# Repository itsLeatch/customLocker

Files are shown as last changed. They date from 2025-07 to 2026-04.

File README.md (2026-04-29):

# customLocker
This project is an electrically locked box. You can safely store things that you are addicted to inside it and unlock it by reaching a particular goal. I'm going to put sweets in it and unlock the box once I've reached my daily calorie target on my smartwatch. Inside the box is a load cell that can roughly detect the amount of sweets taken out. In addition to that, there is a wireless charger, that will charge e.g. your phone while beeing busy. 
## Why I made this project
I often find myself looking at my phone a lot when I'm busy, which slows me down. Furthermore, I also want to do more sport. With the box, I can combine these things and create my first PCB, build a large 3D model, and learn many other skills.
## Showcase
https://github.com/user-attachments/assets/28022000-88c3-4b23-8f9c-2944c17416d4

## Pictures
### 3D-Model


### PCB-Front


### PCB-Back


## Wiring
servo motor: connect the red cable to +5v
hall effect sensor: when facing the smaller side the left once is +5v, the middle one GND and the right one signal
HX711: this board is solderd directly on the PCB in the only possible direction
power: connect the 5V of the USB-C connector with the +5V on the board and the +5V on the wireless charger, same for GND
## BOM
### Aliexpress
| Description | Link | price in USD |
|---|---|---|
| ESP32-32D to control everything | https://de.aliexpress.com/item/4000093185394.html?spm=a2g0o.cart.0.0.b1964ae4QiPiLO&mp=1&gatewayAdapt=glo2deu | 3,56 |
| load cell (5KG AND HX711) to detect the amount of removed items | https://de.aliexpress.com/item/4001274733879.html?spm=a2g0o.cart.0.0.b1964ae4QiPiLO&mp=1&gatewayAdapt=glo2deu | 1,9 |
| 0.96 inch display (white) to display information such as left time, calorien... | https://de.aliexpress.com/item/1005006141235306.html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 | 1,97 |
| servo motor (360°) to lock/open the box | https://de.aliexpress.com/item/1005007173214082.html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 | 1,8 |
| passive buzzer to notify the user | https://de.aliexpress.com/item/1005008825917787.html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 | 1,86 |
| keys (blue) for user inputs | https://de.aliexpress.com/item/1005004341695529.html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 | 1,62 |
| key caps (red) for the keys | https://de.aliexpress.com/item/1005007209930123.html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 | 7,26 |
| wireless charger (b) if the smartphone or simular is in the box | https://de.aliexpress.com/item/1005006386722006.html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 | 5,76 |
| hall effect sensor (47E) to check if the box is open or closed | https://de.aliexpress.com/item/1005008647103022.html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 | 1,8 |
| magnetic tape (10mmx1mm, 1 Meter) for the hall effect sensor | https://de.aliexpress.com/item/1005006757451588.html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 | 2,39 |
| USB-C PCB for power | https://de.aliexpress.com/item/1005009193894473.html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 | 1,15 |
| connector pins (each color) to connect the components to the PCB | https://de.aliexpress.com/item/1005007324368709.html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 | 1,36 |
| some cables (M-F-20pin) to connect the components as well | https://de.aliexpress.com/item/1005007805542492.html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 | 1,24 |
| M4x16mm screws to mount most of the components | https://de.aliexpress.com/item/1005006674812661.html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 | 1,77 |
| m4 threaded inserts (OD 6mm, lenght 6mm) for the screws | https://de.aliexpress.com/item/1005003582355741.html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 | 2,59 |
| M5x30 screws to mount the load cell and the opening mechanism of the box | https://de.aliexpress.com/item/1005006051322108.html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 | 3,26 |
| shipping cost to Germany | | 6,27 |
| total price for ALIEXPRESS | | 47,56 |
### local building center
| Description | price in €  |
|---|---|
| 2 pices M4 DIN9021 to spread the pressure over the box | 2X0,24=0,48 |
| 2 pices M5 DIN9021 to spread the pressure over the box | 2x0,29=0,58 |
| 2 pieces M5 domed cap nut | 2x0,49=0,98 |
| total price in € | 2,04€ |
| total price in $ (7/17/2025 at 4:44pm under: https://www.visa.de/support/verbraucher/visa-reiseservices/exchange-rate-calculator.html)  | 2,39$ |

### PCB from jlcpcp
| Description | price in $ |
|---|---|
| 2 pices M4 DIN9021 to spread the pressure over the box | 4 |
| shipping cost | 3,3 |
| total | 7,3 |

### total cost
| Description | price in $ |
|---|---|
| aliexpress | 47,56 |
| local building center | 2,39 |
| PCB | 7,3 |
| 3D-Filament | nothing - I have to use Printing Legion because I have no 3D-Printer yet 😥 |
| total | **57,25** |

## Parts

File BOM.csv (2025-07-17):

Description | Link | price in USD | Description | price in € | Description | price in $ | Description | price in $
ESP32-32D to control everything | https://de.aliexpress.com/item/4000093185394.html?mp=1 | 3,56 | 2 pices M4 DIN9021 to spread the pressure over the box | 2X0,24=0,48 | 2 pices M4 DIN9021 to spread the pressure over the box | 4 | aliexpress | 47,56
load cell (5KG AND HX711) to detect the amount of removed items | https://de.aliexpress.com/item/4001274733879.html?mp=1 | 1,9 | 2 pices M5 DIN9021 to spread the pressure over the box | 2x0,29=0,58 | shipping cost | 3,3 | local building center | 2,39
0.96 inch display (white) to display information such as left time, calorien... | https://de.aliexpress.com/item/1005006141235306.html?mp=1 | 1,97 | 2 pieces M5 domed cap nut | 2x0,49=0,98 | total | 7,3 | PCB | 7,3
servo motor (360°) to lock/open the box | https://de.aliexpress.com/item/1005007173214082.html?mp=1 | 1,8 | total price in € | 2,04€ |  |  | 3D-Filament | nothing - I have to use Printing Legion because I have no 3D-Printer yet 😥
passive buzzer to notify the user | https://de.aliexpress.com/item/1005008825917787.html?mp=1 | 1,86 | total price in $ (7/17/2025 at 4:44pm under: https://www.visa.de/support/verbraucher/visa-reiseservices/exchange-rate-calculator.html) | 2,39 |  |  | total | 57,25
keys (blue) for user inputs | https://de.aliexpress.com/item/1005004341695529.html?mp=1 | 1,62
key caps (red) for the keys | https://de.aliexpress.com/item/1005007209930123.html?mp=1 | 7,26
wireless charger (b) if the smartphone or simular is in the box | https://de.aliexpress.com/item/1005006386722006.html?mp=1 | 5,76
hall effect sensor (47E) to check if the box is open or closed | https://de.aliexpress.com/item/1005008647103022.html?mp=1 | 1,8
magnetic tape (10mmx1mm, 1 Meter) for the hall effect sensor | https://de.aliexpress.com/item/1005006757451588.html?mp=1 | 2,39
USB-C PCB for power | https://de.aliexpress.com/item/1005009193894473.html?mp=1 | 1,15
connector pins (each color) to connect the components to the PCB | https://de.aliexpress.com/item/1005007324368709.html?mp=1 | 1,36
some cables (M-F-20pin) to connect the components as well | https://de.aliexpress.com/item/1005007805542492.html?mp=1 | 1,24
M4x16mm screws to mount most of the components | https://de.aliexpress.com/item/1005006674812661.html?mp=1 | 1,77
m4 threaded inserts (OD 6mm, lenght 6mm) for the screws | https://de.aliexpress.com/item/1005003582355741.html?mp=1 | 2,59
M5x30 screws to mount the load cell and the opening mechanism of the box | https://de.aliexpress.com/item/1005006051322108.html?utparam-url=scene%3Asearch%7Cquery_from%3A | 3,26
shipping cost to Germany |  | 6,27
total price for ALIEXPRESS |  | 47,56

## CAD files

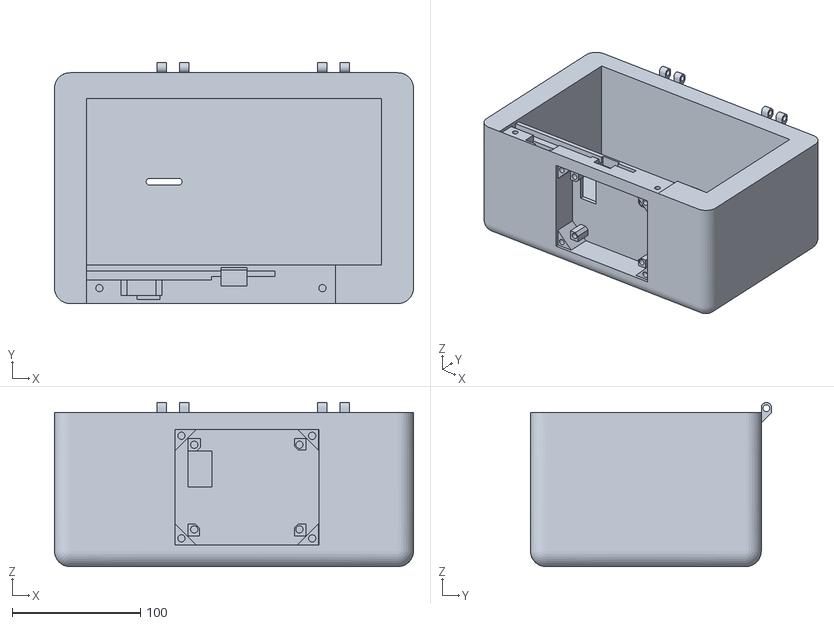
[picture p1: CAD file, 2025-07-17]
models/Box.stl
280.0 x 188.0 x 128.0

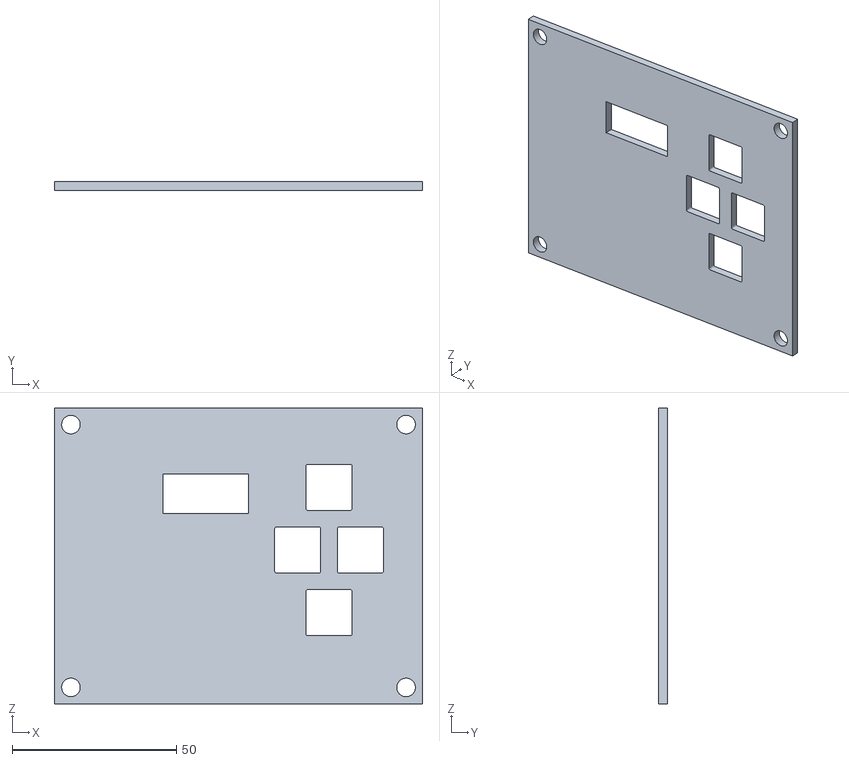
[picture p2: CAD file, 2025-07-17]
models/Front Cover.stl
112.0 x 2.80 x 90.0

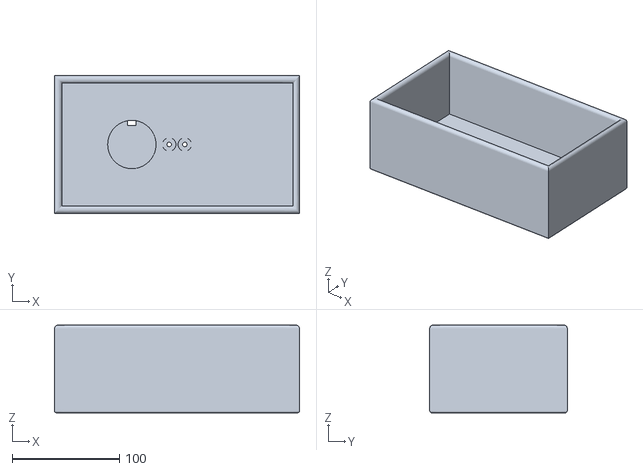
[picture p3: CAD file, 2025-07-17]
models/inner box.stl
228.0 x 128.0 x 81.8

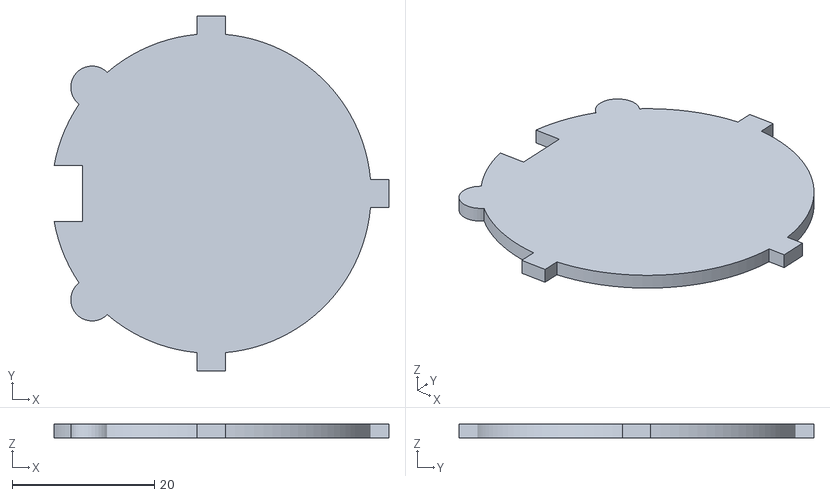
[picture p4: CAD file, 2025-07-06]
models/wireless charger cover.stl
47.2 x 50.0 x 2.00

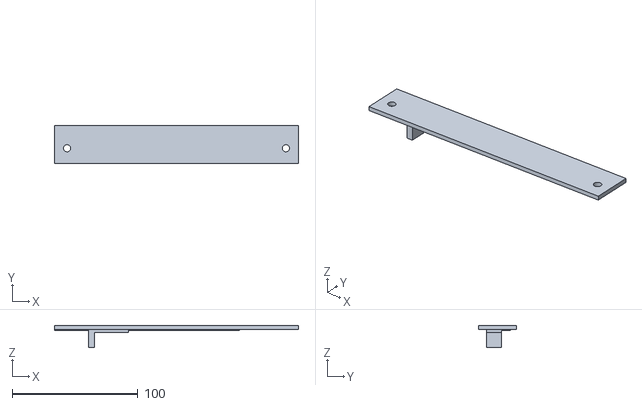
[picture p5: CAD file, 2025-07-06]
models/Gear Cover.stl
194.0 x 30.0 x 17.5

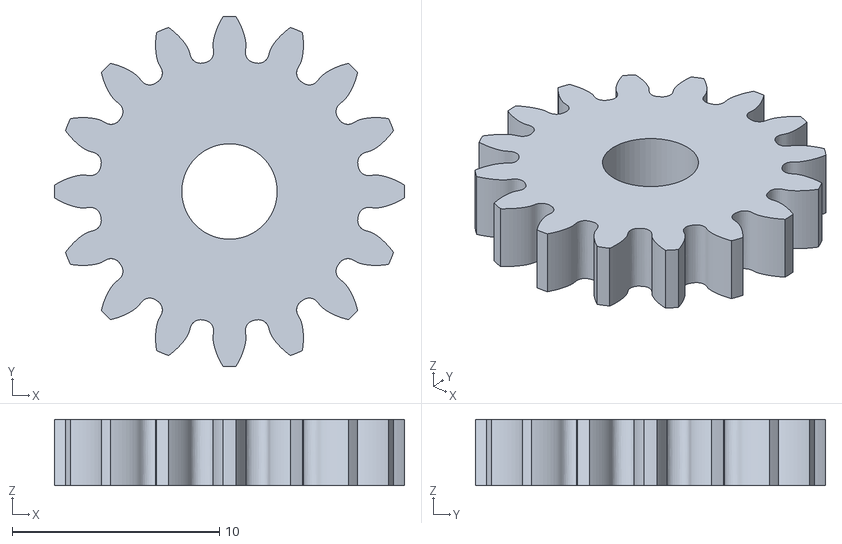
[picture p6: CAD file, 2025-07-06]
models/cog.stl
16.9 x 16.9 x 3.20

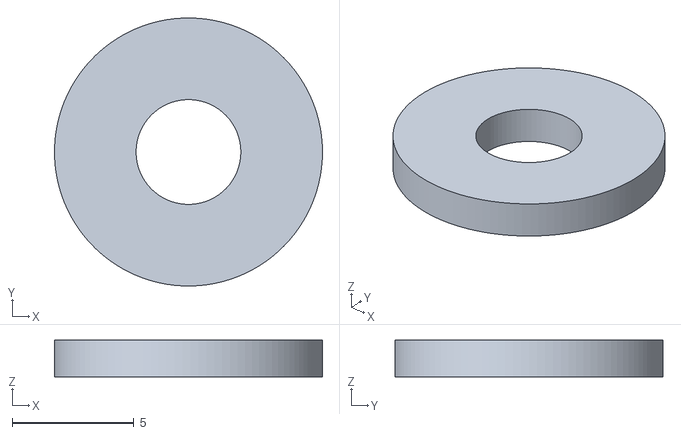
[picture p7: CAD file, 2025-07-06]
models/M4 connector 1.stl
11.0 x 11.0 x 1.50

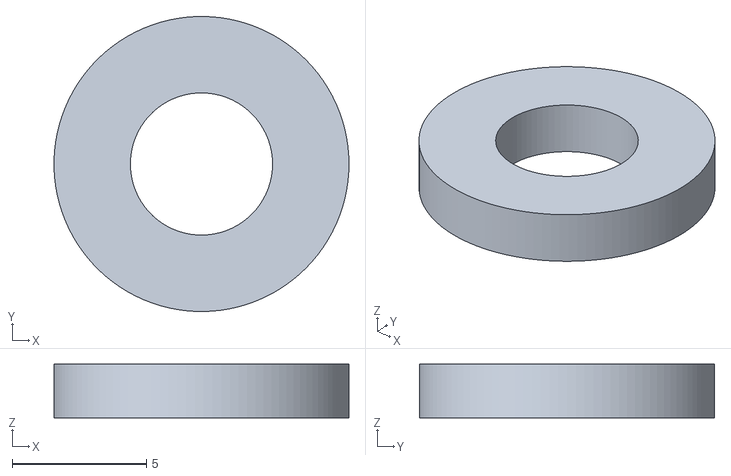
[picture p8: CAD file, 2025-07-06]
models/M5 connector 1.stl
11.0 x 11.0 x 2.00

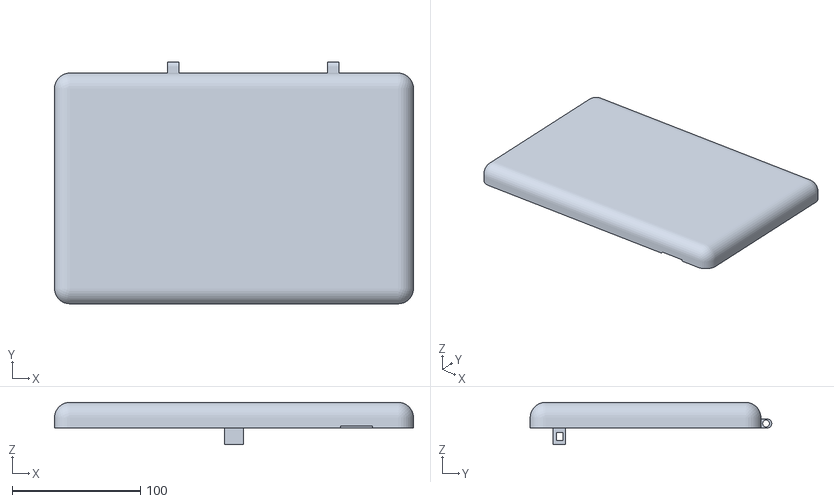
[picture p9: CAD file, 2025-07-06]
models/Box Cover.stl
280.0 x 188.5 x 33.0

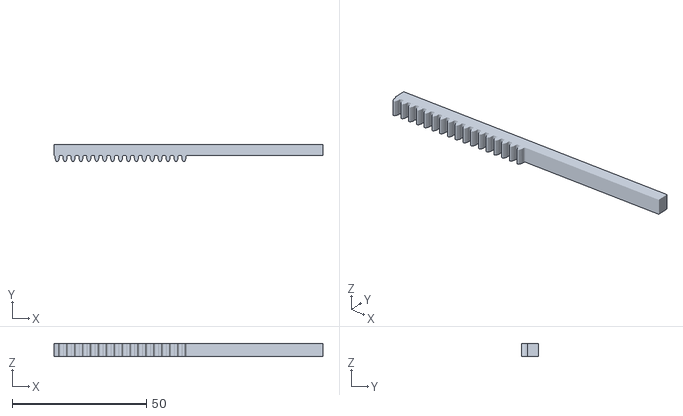
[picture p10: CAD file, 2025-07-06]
models/rack gear.stl
100.0 x 6.24 x 5.00

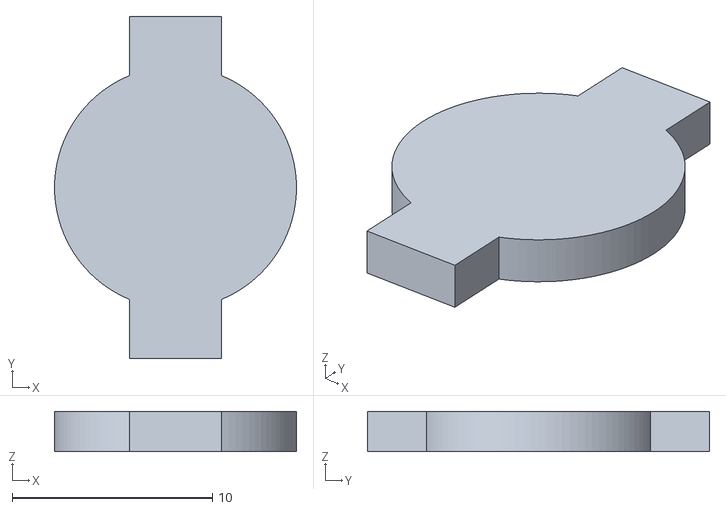
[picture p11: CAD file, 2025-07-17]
models/screw cover 1.stl
12.1 x 17.1 x 2.00

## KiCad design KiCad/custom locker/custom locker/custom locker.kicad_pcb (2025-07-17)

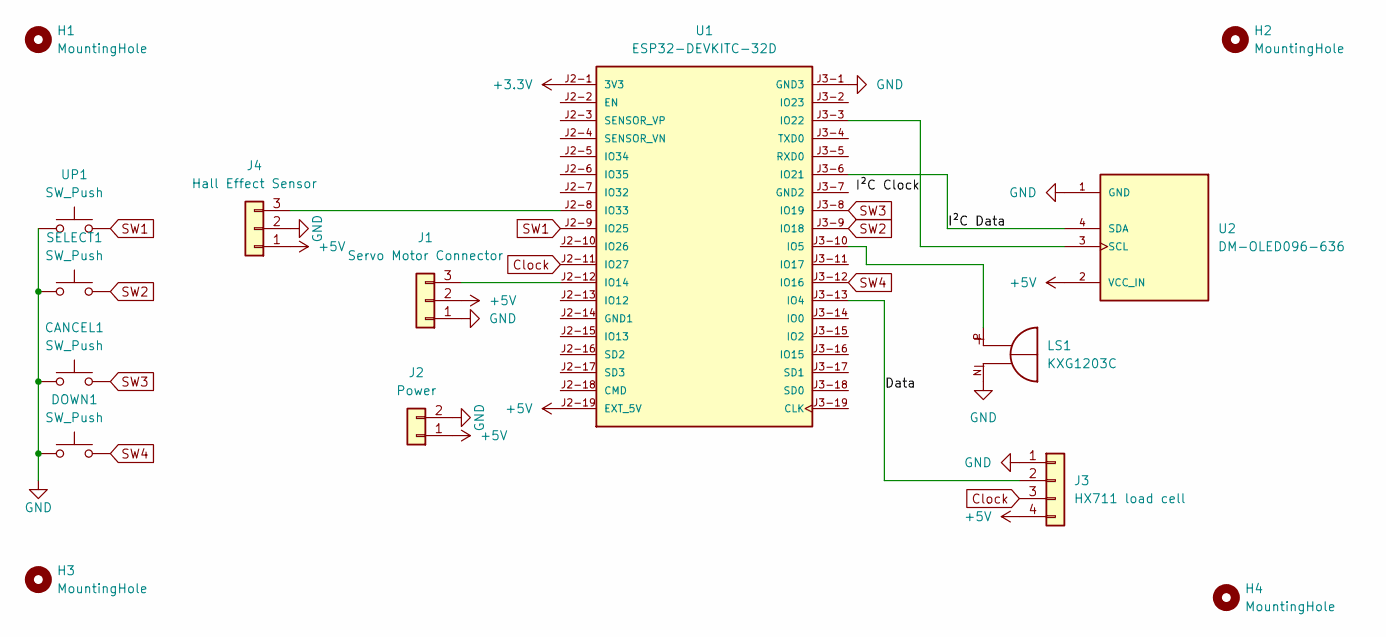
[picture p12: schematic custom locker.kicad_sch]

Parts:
CANCEL1: SW_Push; SW_Cherry_MX_1.00u_PCB
DOWN1: SW_Push; SW_Cherry_MX_1.00u_PCB
H1, H2, H3, H4: MountingHole; MountingHole_4.3mm_M4
J1: Servo Motor Connector; PinHeader_1x03_P2.54mm_Vertical
J2: Power; PinHeader_1x02_P2.54mm_Vertical
J3: HX711 load cell; PinHeader_1x04_P2.54mm_Vertical
J4: Hall Effect Sensor; PinHeader_1x03_P2.54mm_Vertical
LS1: KXG1203C; XDCR_KXG1203C; PARTREV 1.3
SELECT1: SW_Push; SW_Cherry_MX_1.00u_PCB
U1: ESP32-DEVKITC-32D; MODULE_ESP32-DEVKITC-32D; PARTREV V4
U2: DM-OLED096-636; MODULE_DM-OLED096-636; PARTREV 2018-09-10
UP1: SW_Push; SW_Cherry_MX_1.00u_PCB

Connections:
+3.3V: U1.J2-1 (3V3)
+5V: J1.2, J2.1, J3.4, J4.1, U1.J2-19 (EXT_5V), U2.2 (VCC_IN)
/Data: J3.2, U1.J3-13 (IO4)
/I²C Clock: U1.J3-3 (IO22), U2.3 (SCL)
/I²C Data: U1.J3-6 (IO21), U2.4 (SDA)
Clock: J3.3, U1.J2-11 (IO27)
GND: CANCEL1.1, DOWN1.1, J1.1, J2.2, J3.1, J4.2, LS1.N, SELECT1.1, U1.J3-1 (GND3), U2.1 (GND), UP1.1
unnamed: J1.3, U1.J2-12 (IO14)
unnamed: J4.3, U1.J2-8 (IO33)
unnamed: LS1.P, U1.J3-10 (IO5)
SW1: U1.J2-9 (IO25), UP1.2
SW2: SELECT1.2, U1.J3-9 (IO18)
SW3: CANCEL1.2, U1.J3-8 (IO19)
SW4: DOWN1.2, U1.J3-12 (IO16)

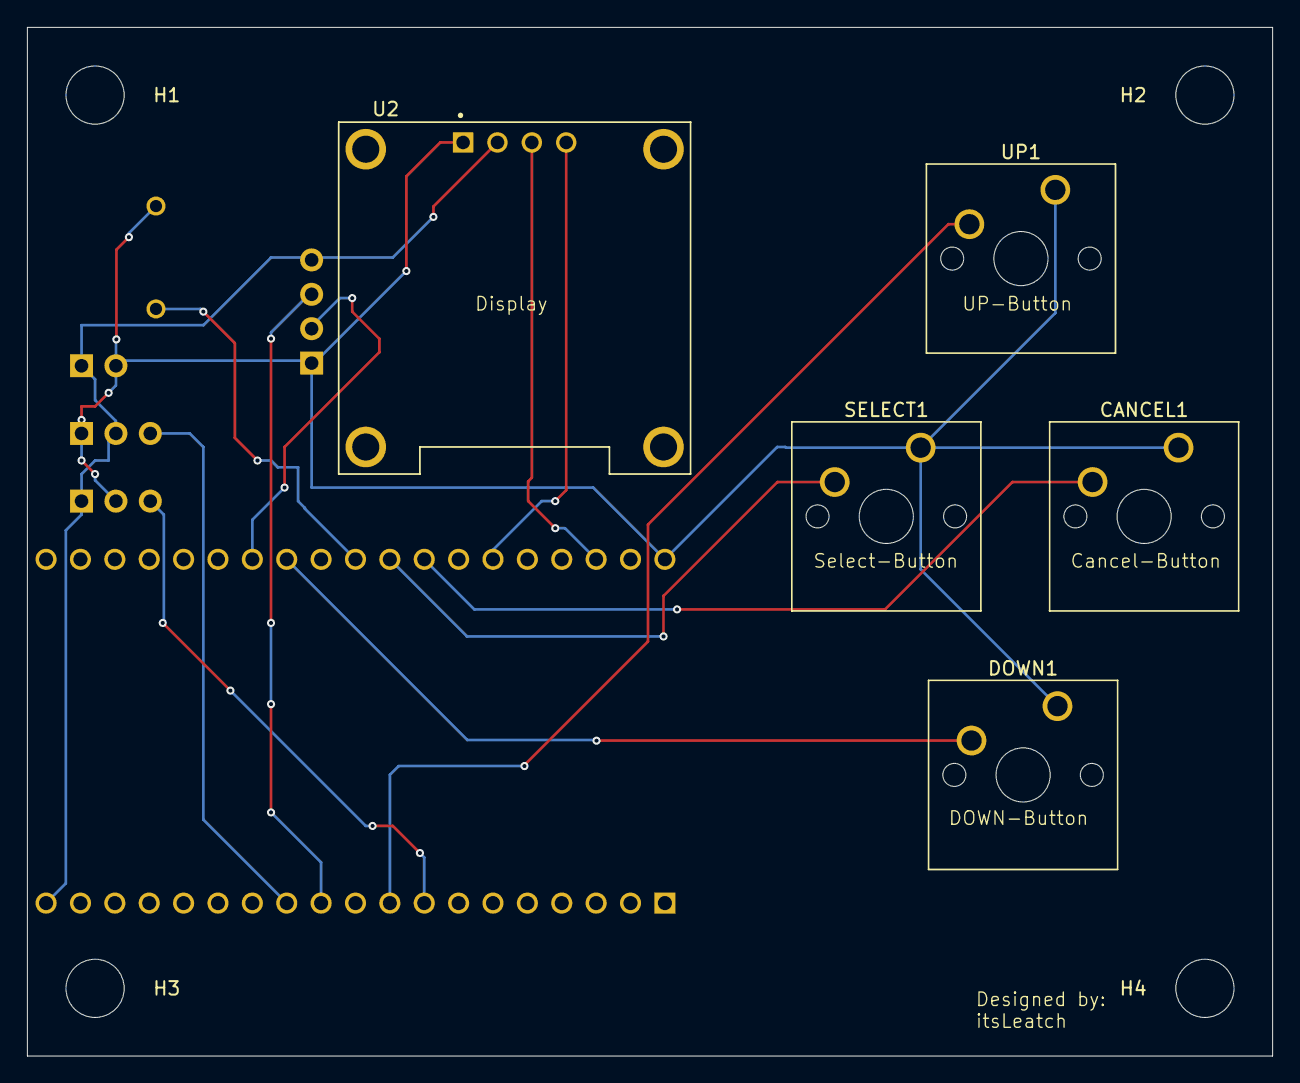
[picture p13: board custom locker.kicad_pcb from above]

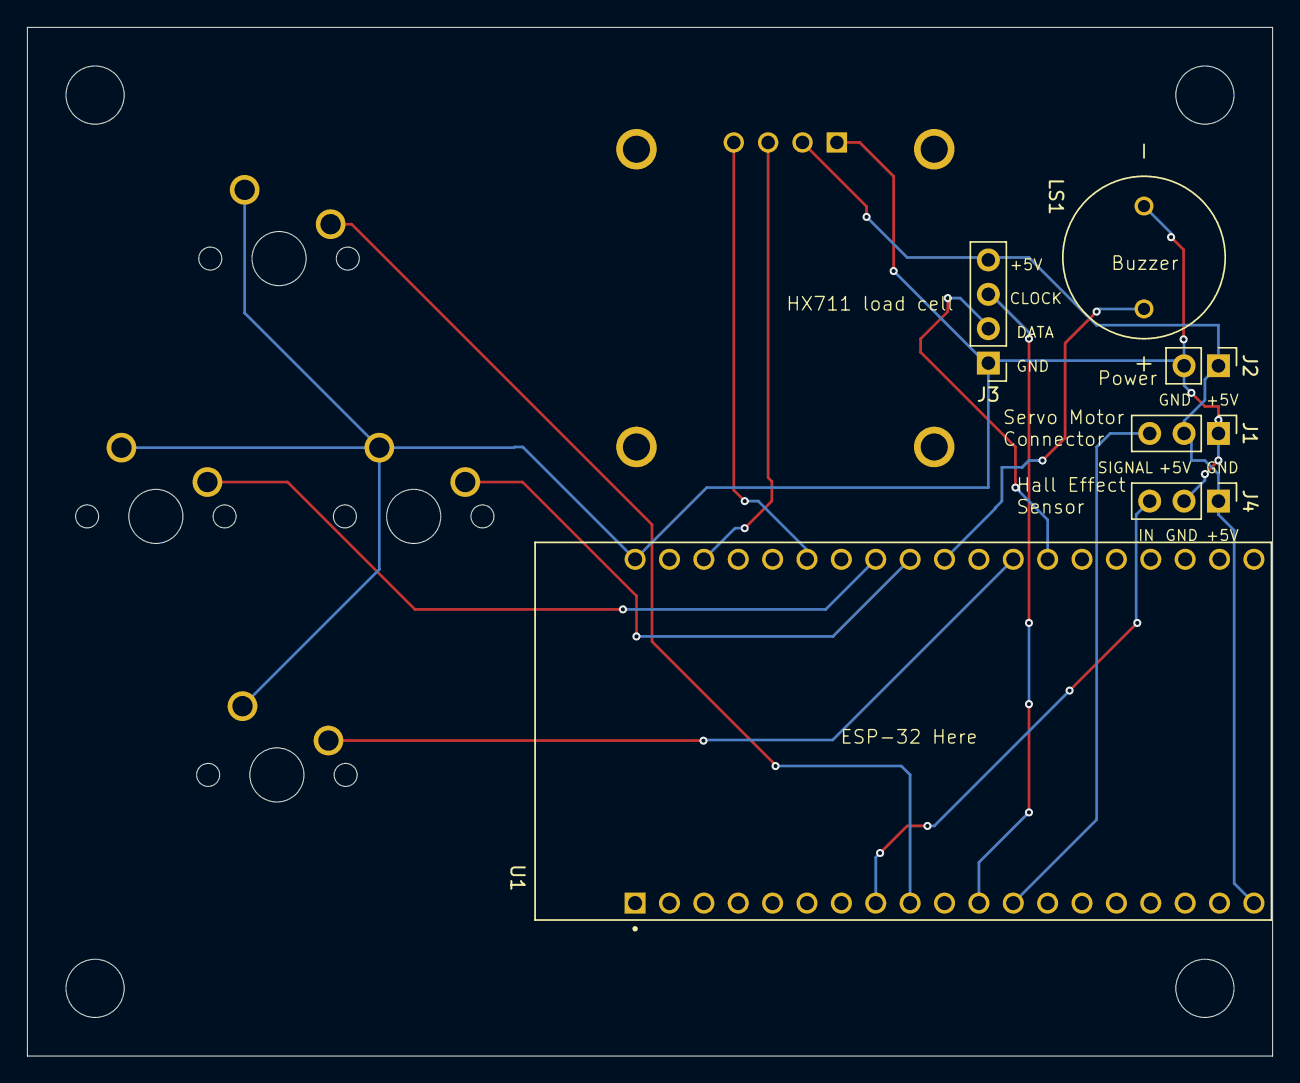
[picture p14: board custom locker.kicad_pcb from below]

Board: 2 copper layers, 92.0 x 76.0 mm, 15 parts (6 on the bottom side), 13 nets.

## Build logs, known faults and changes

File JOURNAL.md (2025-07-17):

---
title: "custom locker"
author: "itsLeatch"
description: "It's an electrically locked box that only opens once you've reached your goal."
created_at: "2025-06-09"
---
**Total time spent: 56h**

# Day 1 (June 9th): Familiarize yourself with fusion 360
Today I created an education account for fusion 360 and installed the application as well. In addition to that, I familiarized myself with the program by building a lego brick from an tuturial. 


**Time spent: 3h**
# Day 2 (June 12th): First steps in KiCad
Today I installed KiCad and followed the tutorial from [Hackpad](https://hackpad.hackclub.com/guide). I also decided for the [ESP32-32D](https://de.aliexpress.com/item/4000093185394.html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), added the three-pin connector for the servo and I was looking for a screen. However I am still unsure about the measurements of the footprint.

**Time spent: 3h**

# Day 3 (June 26th): A lot of porgress for the PCB
On day three, I worked a lot. Firstly, I spent some time searching for a good way to implement audio. Then I realised that I didn't need a fancy audio source with an amplifier. I opted for a simple active buzzer. Next, I looked for some buttons and ended up with Hackpad-like keyboard switches to control the box later on. I also did a lot of research on load cells. I will use an HX711 chip for the load cell. Tomorrow, I need to find the exact measurements of the cell for the box. I also created a schematic diagram and moved some parts to the back of the PCB. Tomorrow, I have to wire the PCB and perhaps create the BOM on GitHub. Overall, I am really happy with today's progress.
### The wired schema:

### The current PCB-state:
front:

back:

**Time spent: 8h**

# Day 4 (July 1st): Finished PCB (hopefully)
I was really busy today. I added a fourth switch and wired the PCB.

I also started the 3D modelling of the box and went to a local building centre to look at the prices of screws.

I am also quite confident with my selected parts. A boom will follow shortly. 

**Time spent: 12h**

# Day 5 (July 2nd): PCB-Housing
On day 5, I mainly worked on the PCB housing for the box. I created screw holders and a front plate for installation, as well as cut-outs for components and the hall effect sensor.
Front-Cover:

Cut-Outs:

with PCB:

**Time spent: 4h**

# Day 6 (July 3nd): Closing-Mechanism
Today I started creating the closing mechanism. First I added the housing for the servo motor.
servo motor housing:

Afterwards I started creating the gear system.
gear system:

**Time spent: 2h**

# Day 7 (July 5nd): Closing-Mechanism
Today I made a lot of progress. I added motion to the gear and a gear cover to hold the servo.

Afterwards I created the distance holder for the load cell as well as a model of the laod cell and the inner box that carries the weight. 

**Time spent: 8h**

# Day 8 (July 6nd): Closing-Mechanism
Today I added a Box cover with some hinges.

Then I added the final part to close the box.

Afterwards I made the hole for the wireless charger.

I also had to add a lot of details with regard to spacing, which was really time-consuming.
**Time spent: 10h**

# Day 9 (July 17nd): Final
I forgot that the screws would stick out a little, so I made a hole for them with covers.

There were also some other minor improvements that are not worth mentioning.
Besides that, I spent most of the time working on all the files to submit the project finally. 🎆
**Time spent: 6h**

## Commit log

2025-06-26 add KiCad Project for Day3
    [custom locker.kicad_pcb, custom locker.kicad_sch]
2025-07-01 finished pcb
    [custom locker.kicad_pcb, custom locker.kicad_sch]
2025-07-01 PCB wiring
    [custom locker.kicad_pcb, custom locker.kicad_sch]
2025-07-01 little changes on PCB
    mainly added screw holes
    [custom locker.kicad_pcb, custom locker.kicad_sch]
2025-07-06 small PCB changes
    [custom locker.kicad_pcb]
2025-07-06 added all the files
    [Box Cover.stl, Box.stl, Front Cover.stl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]
2025-07-17 final submission files
    [cog.stl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]
2025-07-17 small improvments and the bom as csv
    [BOM.csv, Box.stl, Front Cover.stl]
